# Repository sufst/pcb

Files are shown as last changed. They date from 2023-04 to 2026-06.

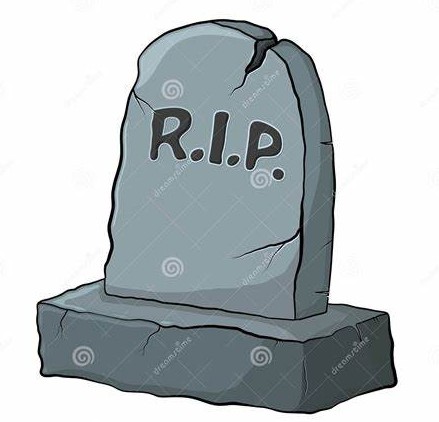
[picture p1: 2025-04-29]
common/images/RIP.jpg

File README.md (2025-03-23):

# PCBs

## About
Central repository of all schematics and PCB design files.

| Folder | Project | Project Code |
|---|---|---|
| ail | Accumulator Indicator Light Logic| `ail` |
| ail-led | Accumulator Indicator Light Led  | `ail-led` |
| batak | Batak Game (non-car) | `batak` |
| break-light| Rear Break Light | `break-light`|
| bspd | Brake System Plausibility Device | `bspd` |
| can-node | Voltage Reader and Broadcaster | `can-node` |
| curr-amp | Current Sensor Amplifier | `curr-amp` |
| dash | Dashboard | `dash` |
| discharge  | Discharge Relay Breakout | `discharge`  |
| hv-sense | High Voltage Sense | `hvs` |
| latching | Latch Circuit | `latching` |
| loom* | Loom Design | `loom` |
| lvbms | Low Voltage Battery Management System | `lvbms` |
| precharge  | Precharge Controller | `precharge`  |
| segment | Segment | `segment` |
| telemetry  | On-Car Telemetry | `telemetry`  |
| test-rig | PCB Test / Demo Rig | `test` |
| top-level* | Full Car Schematic | |
| trc | TSAC Relay Controller | `trc` |
| tsal | Tractive System Active Light | `tsal` |
| vcu | Vehicle Control Unit | `vcu` |

We design our PCBs in KiCad (version 8+).

>*Moved to https://github.com/sufst/loom

## Version Control for KiCad Projects

### Why?
- Revert individual changes.
- Document development history via commits and GitHub issues.
- Easily view previous versions of designs.
- Manage shared library of components.

### Files

Files that should be in this repo, under version control:
- Project files (`.kicad_pro`).
- Schematic files (`.kicad_sch`).
- PCB files (`.kicad_pcb`).
- Custom footprints (`.kicad_mod`).
- Custom symbols (`.kicad_sym`).
- Footprint library tables (`fp-lib-table`).
- Symbol library tables (`sym-lib-table`).
- 3D models of components (`.step` files).
- Simulation code (e.g. `.asc` files from LTSpice).

Files that should never be in here:
- Exports such as BOMs, gerbers, netlists, renders, etc.
- Local project settings (`.kicad_prl`).
- Project backups (.zip files generated in `<project name>-backups`, `.bak` `.bck` `-bak` files).
- Cache files (`fp-info-cache`).

The `.gitignore` should prevent the addition of files we don't want to keep in here, but before you commit make sure to do a quick check of what is actually being added.

### Shared Resources

The `common` folder is used for resources which can be shared across multiple projects. This includes:

- Images (`images` subdirectory).
- 3D models (`step` subdirectory).
- Custom symbols (`sufst-lib.kicad_sym`).
- Custom footprints (`sufst-lib.pretty`).
- SUFST standard sheet layout (`sheet-layout.kicad_wks`).

> Note: Since projects were previously in their own individual repos, many designs still have their own libraries, step files, etc. These will gradually be migrated to the SUFST library.

### Library Paths
When you configure the library paths for a project (`sym-lib-table` and `fp-lib-table` data), make sure to always use a path relative to the project with the `${KIPRJMOD}` substitution.

- Correct: `${KIPRJMOD}/../common/sufst-lib.kicad_sym`
- Incorrect: `/Users/<your name>/Documents/sufst/pcb/common/sufst-lib.kicad_sym`

If an absolute path is used, when someone else opens the project that path will not exist and the library paths will not be valid. `-lib-table` files should never contain an absolute path.

### Git Limitations
It is not possible to resolve merge conflicts within individual design files, which is an unfortunate limitation of using `git` with KiCad. While KiCad files are in a text format, they aren't really designed to be edited manually. It is therefore *essential* that only one person is editing a particular file in a project at a time (including the shared library). Once someone starts working on a file, until it is merged into the `main` branch nobody else can edit that file. A good way to get round this is to use the "hierarchical sheets" feature to divide schematics into multiple files (if it can be done in a logical way).

## Releases

### Release Files
When a PCB is fabricated, a new 'release' for the given project should be 
created and stored within this repo in the `releases/<PROJECT NAME>` folder. 
This folder should contain the latest version (and ONLY the latest version) of
the following files:

1. Exported gerbers and drill files in a ZIP archive called `fabrication.zip`.
2. Schematic sheets as a PDF (`Schematic.pdf`).
3. Layout as a PDF in colour, with border and title block (`Layout.pdf`).
4. HTML iBOM created using the ["Interactive HTML BOM Plugin"](https://github.com/openscopeproject/InteractiveHtmlBom) (`ibom.html`).

Additionally, a file called `info` (no extension) should be created (if it 
doesn't already exist) containing release information in the following format:

```txt
version: <VERSION NUMBER>
date: <RELEASE DATE>
fabrication: <COMPANY>
```

Version numbers should be in the format `v1.0.1` and dates should be in the
format `YYYY-MM-DD`. For example:

```txt
version: v1.0.1
date: 2023-01-23
fabrication: JLCPCB
```

The release folder for a project should then have the following structure and 
file names:

```txt
<PROJECT NAME>
├── Layout.pdf
├── Schematic.pdf
├── fabrication.zip
├── ibom.html
└── info
```

When creating a new release, make sure to overwrite/replace all the existing 
files.

### Release Tag

The release commit should then be tagged with the following command:

```sh
git tag <PROJECT CODE>-<VERSION_NUMBER>
```

Tagging should be done **after** merging to `main`! Example command:

```sh
git tag segment-v1.0.1
```

To push tags to GitHub:

```sh
git push --tags
```

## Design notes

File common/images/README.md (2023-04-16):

These images can be used to add SUFST graphics to PCB silkscreens using KiCad's bitmap2component app.

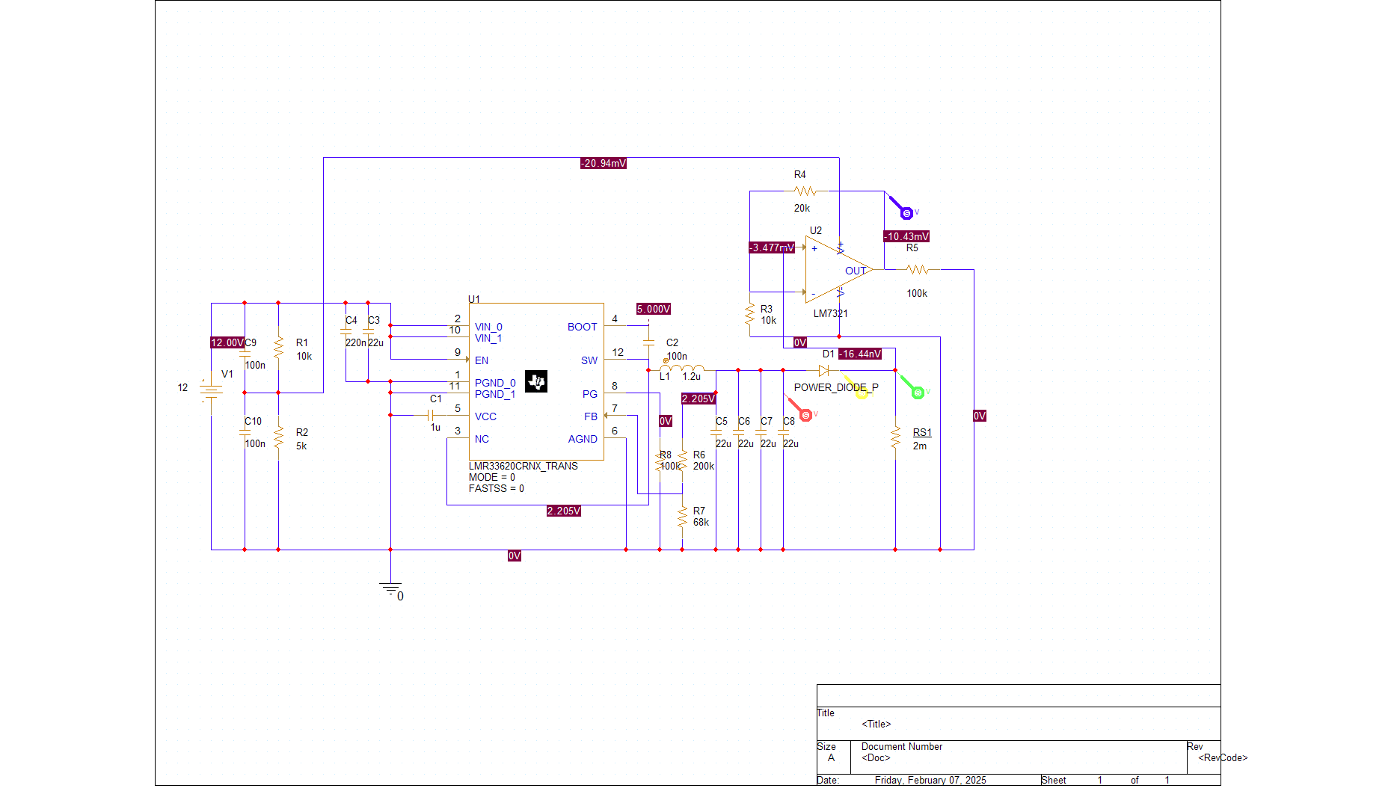
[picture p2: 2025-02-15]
tsal-led/sim/Pspice/tsal-led-driver/TSAL-LED-DRIVER.png

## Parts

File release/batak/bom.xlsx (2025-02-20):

Reference | Value | Datasheet | Footprint | Qty | Supplier | URL | Order Qty | Total Cost (£) | Notes
C1,C4 | 1uF | ~ | Capacitor_SMD:C_0603_1608Metric | 2 | Mouser |  |  |  | Already owned?
C2 | 10nF | ~ | Capacitor_SMD:C_0603_1608Metric | 1 | Mouser |  |  |  | Already owned?
C3,C8,C10 | 10uF | ~ | Capacitor_SMD:C_0603_1608Metric | 3 | Mouser |  |  |  | Already owned?
C5 | 470uF | ~ | Capacitor_THT:CP_Radial_D10.0mm_P5.00mm | 1 | Mouser | https://www.mouser.co.uk/ProductDetail/Vishay-BC-Components/MAL219056471E3 | 2 | 3.6 | Already owned?
C6,C9 | 100nF | ~ | Capacitor_SMD:C_0603_1608Metric | 2 | Mouser |  |  |  | Already owned?
C7 | 100uF | ~ | Capacitor_SMD:C_0603_1608Metric | 1 | Mouser |  |  |  | Already owned?
C11 | 180uF | ~ | Capacitor_THT:CP_Radial_D8.0mm_P3.50mm | 1 | Mouser | https://www.mouser.co.uk/ProductDetail/KEMET/A759KR187M1VAAE024 | 2 | 1.02 | Already owned?
D1 | YELLOW | ~ | LED_SMD:LED_0603_1608Metric | 1 | Mouser |  |  |  | Already owned?
D2 | GREEN | ~ | LED_SMD:LED_0603_1608Metric | 1 | Mouser |  |  |  | Already owned?
D3,D4,D6 | ESD9B3.3ST5G | https://www.onsemi.com/pub/Collateral/ESD9B-D.PDF | Diode_SMD:D_0603_1608Metric | 3 | Mouser | https://www.mouser.co.uk/ProductDetail/onsemi/ESD9B3.3ST5G?qs=yU2N9dt%252BrfmXrPf3vhgUEA%3D%3D | 10 | 0.76
D5 | BAT54W | https://assets.nexperia.com/documents/data-sheet/BAT54W_SER.pdf | Package_TO_SOT_SMD:SOT-323_SC-70 | 1 | Mouser | https://www.mouser.co.uk/ProductDetail/Taiwan-Semiconductor/BAT54W-RFG?qs=KwaGCOX4wIZBOfr1Otvg1A%3D%3D | 5 | 0.55 | Already owned?
IC1,IC2 | HT16K33 | https://www.holtek.com/webapi/116711/HT16K33Av101.pdf | sufst-lib:HT16K33 | 2 | AliExpress | https://www.aliexpress.com/item/1005007501060086.html | 5 | 3.79
J1 | USB_C_Receptacle_USB2.0_16P | https://www.usb.org/sites/default/files/documents/usb_type-c.zip | Connector_USB:USB_C_Receptacle_GCT_USB4105-xx-A_16P_TopMnt_Horizontal | 1 | Mouser | https://www.mouser.co.uk/ProductDetail/GCT/USB4105-GF-A-120?qs=QNEnbhJQKva%252Bjxw%2FpEjDhQ%3D%3D | 3 | 2.34
J2,J3,J4,J5,J6,J7,J8,J9,J10,J11,J12,J13 | Conn_01x04 | ~ | Connector_Molex:Molex_KK-254_AE-6410-04A_1x04_P2.54mm_Vertical | 13 |  |  |  |  | Already owned?
J14 | Conn_01x02 | https://docs.rs-online.com/accf/A700000008956731.pdf | Connector_AMASS:AMASS_XT60PW-F_1x02_P7.20mm_Horizontal | 1 |  |  |  |  | Already owned?
L1 | 68uH | ~ | Inductor_SMD:L_Coilcraft_MSS1210-XXX | 1 | Mouser | https://www.mouser.co.uk/ProductDetail/Coilcraft/MSS1210-683MED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 | 3 | 9.6
Q1,Q2 | NPN | https://ngspice.sourceforge.io/docs/ngspice-html-manual/manual.xhtml#cha_BJTs | Package_TO_SOT_SMD:SOT-23 | 2 | AliExpress | https://www.aliexpress.com/item/1005007360183764.html | 50 | 2.42 | 50PCS-SS8050-Y1
Q3,Q4,Q5,Q6,Q7,Q8,Q9,Q10,Q11,Q12,Q13,Q14,Q15,Q16,Q17 | NMOS | https://www.diodes.com/assets/Datasheets/ds11303.pdf | Package_TO_SOT_SMD:SOT-23 | 15 | AliExpress | https://www.aliexpress.com/item/1005006109969648.html | 100 | 2.44 | need to check voltage drop + current rating of specific model
R1,R2 | 1k | ~ | Resistor_SMD:R_0603_1608Metric | 14 | Mouser |  | 100 | 0.65 | Already owned?
R3,R4,R5,R8,R9,R22,R23,R24,R25,R26,R27,R28,R29,R30,R31,R32,R33,R34,R35,R36,R37 | 10k | ~ | Resistor_SMD:R_0603_1608Metric | 21 | Mouser |  | 100 | 0.65 | Already owned?
R6,R7 | 5.1k | ~ | Resistor_SMD:R_0603_1608Metric | 2 | Mouser |  | 100 | 0.65 | Already owned?
R10,R11,R12,R13,R14,R15,R16,R17,R18,R19,R20,R21,R38,R39 | 51k | ~ | Resistor_SMD:R_0603_1608Metric | 14 | Mouser |  | 100 | 0.65 | Already owned?
SW1,SW2 | BOOT, RESET | ~ | Button_Switch_SMD:SW_Push_1P1T_NO_CK_KMR2 | 2 |  |  |  |  | Already owned (for LVBMS)?
U1 | AP2112K-3.3 | https://www.diodes.com/assets/Datasheets/AP2112.pdf | Package_TO_SOT_SMD:SOT-23-5 | 1 | AliExpress | https://www.aliexpress.com/item/32998839398.html | 10 | 1.01
U2 | CH340C | https://datasheet.lcsc.com/szlcsc/Jiangsu-Qin-Heng-CH340C_C84681.pdf | Package_SO:SOIC-16_3.9x9.9mm_P1.27mm | 1 | AliExpress | https://www.aliexpress.com/item/1005006040438712.html | 5 | 1.87
U3 | XL1509-5.0 | https://datasheet.lcsc.com/lcsc/1809050422_XLSEMI-XL1509-5-0E1_C61063.pdf | Package_SO:SOIC-8_3.9x4.9mm_P1.27mm | 1 | AliExpress | https://www.aliexpress.com/item/1005003830233152.html | 10 | 1.2
U4 | ESP32-S3-WROOM-1 | https://www.espressif.com/sites/default/files/documentation/esp32-s3-wroom-1_wroom-1u_datasheet_en.pdf | RF_Module:ESP32-S3-WROOM-1 | 1 | Mouser | https://www.mouser.co.uk/ProductDetail/Espressif-Systems/ESP32-S3-WROOM-1-N16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 | 3 | 8.25 | Must be specifically the ESP32-S3-WROOM-1-N8 or ESP32-S3-WROOM-1-N16
U5,U6 | LTC-4627JR | http://optoelectronics.liteon.com/upload/download/DS30-2000-185/LTC-4627JR.pdf | Display_7Segment:LTC-4627Jx | 2 | Mouser | https://www.mouser.co.uk/ProductDetail/Lite-On/LTC-4627JR?qs=WxFF5lh7QM3%252BoGt5Rn2nWQ%3D%3D | 4 | 6.6
BZ1 | Buzzer | https://www.mouser.co.uk/datasheet/2/1628/cmi_1275_03th-3513223.pdf | sufst-lib:CUI_CMI-1275-85T | 1 | Mouser | https://www.mouser.co.uk/ProductDetail/Same-Sky/CMI-1275-03TH?qs=olJun0bQHM%252BIti8gD3qf0w%3D%3D | 3 | 2.34 | Already owned (Adam's kit)?
RV1 | 300k | https://www.mouser.co.uk/datasheet/2/54/3362-776956.pdf | sufst-lib:TRIM_3362P-1-304LF | 1 | Mouser | https://www.mouser.co.uk/ProductDetail/Bourns/3362P-1-304LF?qs=P4Be%2F1I712%2FfO%252BvhxotFeA%3D%3D | 3 | 2.58 | Already owned (for BPSD)?
SW3 | 0S102011MS2QN1 | https://www.ckswitches.com/media/1428/os.pdf | sufst-lib:0S102011MS2QN1 | 1 | Mouser | https://www.mouser.co.uk/ProductDetail/CK/0S102011MS2QN1?qs=xWNScUPc28o71osWFQSpZA%3D%3D | 3 | 1.08 | Already owned?
- | LED Buttons |  |  | 12 | AliExpress |  | 12 | 45 | 100mm or 60mm?
- | Start/Reset Buttons |  |  | 2 |  |  |  |  | Also needed for dash?

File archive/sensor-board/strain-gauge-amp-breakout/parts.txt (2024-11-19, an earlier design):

https://www.mouser.co.uk/ProductDetail/Texas-Instruments/REF2033AIDDCR?qs=7z%252BmIopC6%2FKHHOBVNaL7UQ%3D%3D
https://www.mouser.co.uk/ProductDetail/Analog-Devices/AD623ARMZ-REEL

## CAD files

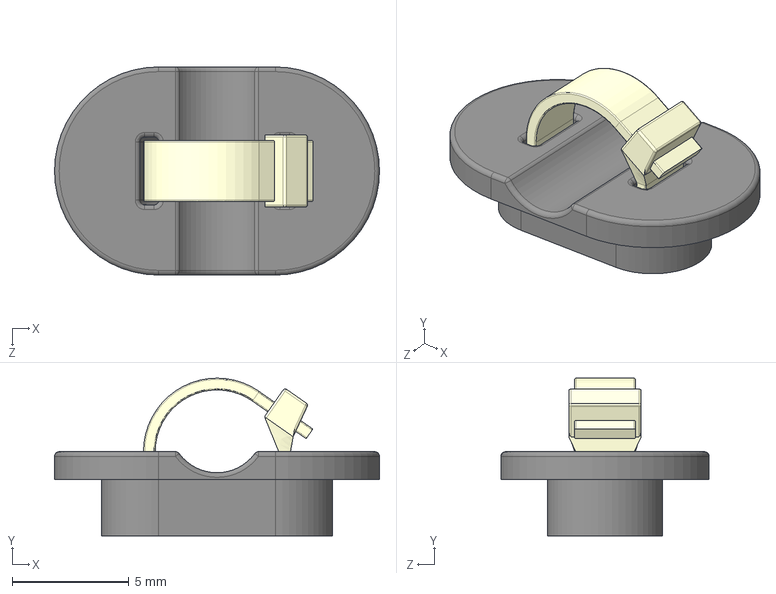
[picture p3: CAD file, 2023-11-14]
PCB - VOLTAGE TAPS/segment-pcb-ty-rap-assy.STEP
13.9 x 6.74 x 8.90 mm
segment-pcb-ty-rap-mount
segment-pcb-ty-rap

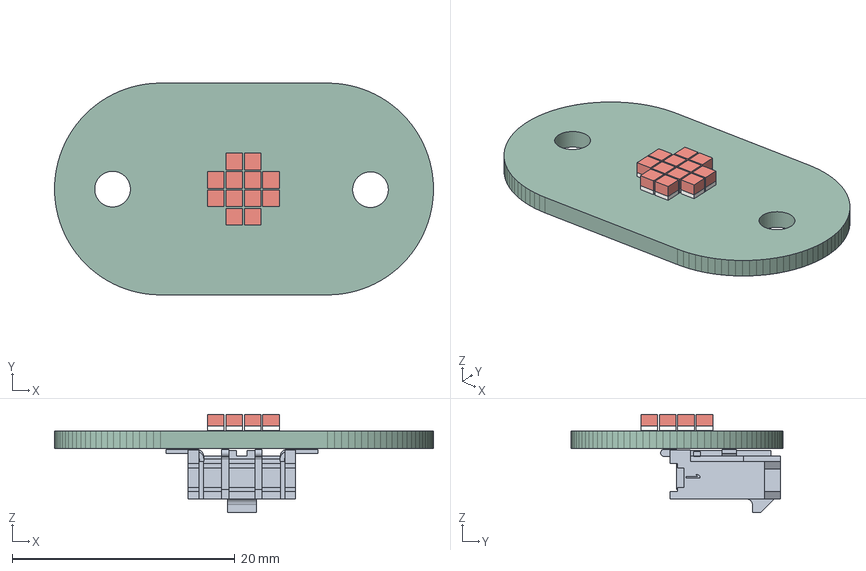
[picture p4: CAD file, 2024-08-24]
ail-LED/ail-LED.step
34.0 x 19.0 x 8.79 mm
(Unsaved) x 12
ail-LED PCB

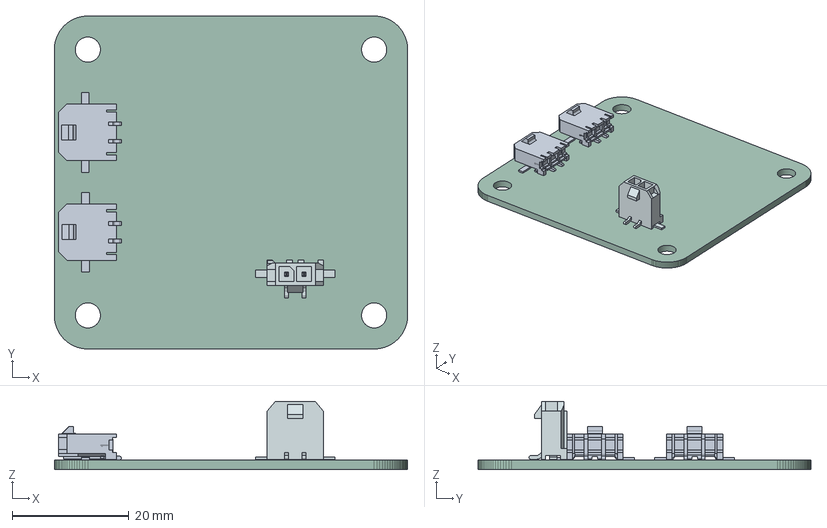
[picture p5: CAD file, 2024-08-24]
ail/ail.step
60.5 x 57.0 x 11.7 mm
436500224wbm000_01
ail PCB

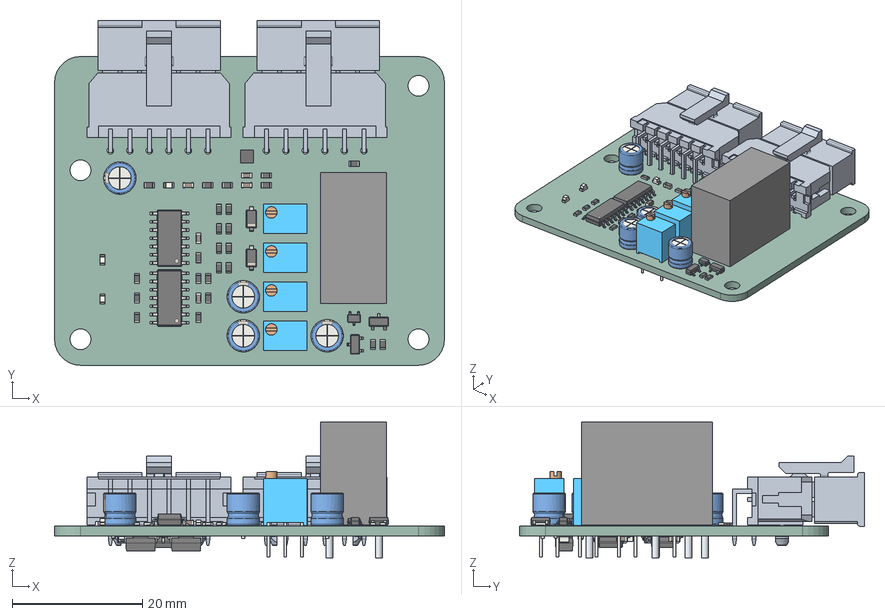
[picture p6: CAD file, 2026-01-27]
bspd/bspd v1.3.0.step
60.0 x 53.0 x 20.9 mm
R_0603_1608Metric x 32
D_SOD-123 x 2
CP_Radial_D5.0mm_P2.00mm x 4
SOT-323_SC-70 x 2
Potentiometer_Bourns_3266W_Vertical x 4
C_0603_1608Metric x 8
Leads
LED_0603_1608Metric x 3
SOIC-14_3.9x8.7mm_P1.27mm x 4
SOT-23 x 2
D_SMA x 2
BSPD_PCB

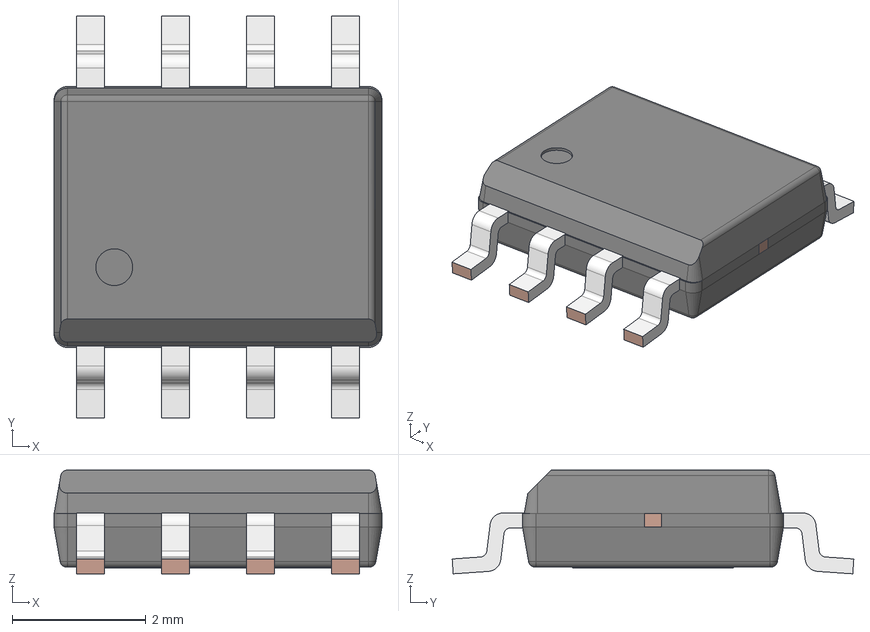
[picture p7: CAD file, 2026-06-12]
common/step/AP7375Q-33SP-13.stp
4.90 x 6.00 x 1.55 mm
CPD
LDF - outer lead
LDF - 8L-EP

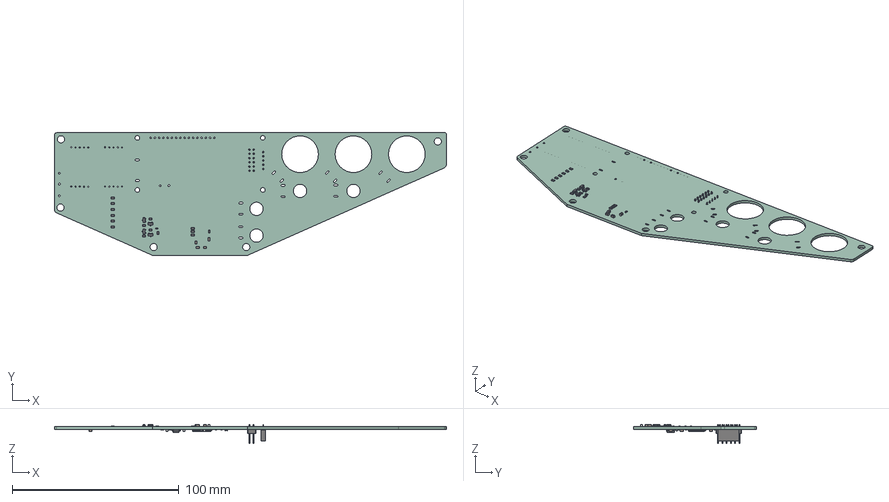
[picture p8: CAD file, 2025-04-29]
dash/Dash-PCB.step
235.0 x 73.6 x 11.6 mm
R_0805_2012Metric x 25
C_0805_2012Metric x 10
SOT_23 x 4
Fuse_0603_1608Metric x 2
PinHeader_2x06_P254mm_Vertical
C_0603_1608Metric x 3
SOIC_8_39x49mm_P127mm
TQFP_44_10x10mm_P08mm
PinSocket_1x05_P254mm_Vertical
Dash-PCB_PCB

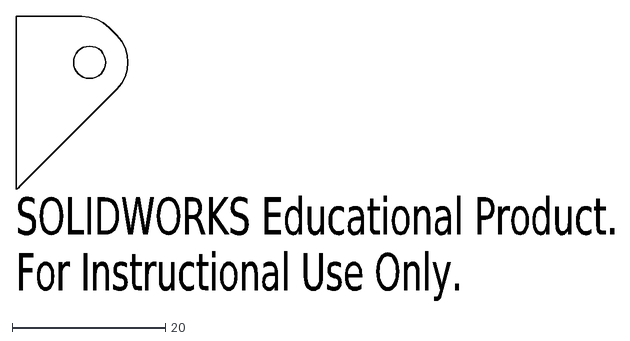
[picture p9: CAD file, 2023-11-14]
PCB - VOLTAGE TAPS/24-A02-212-0 - PART - THIN BUSBAR RH HOLE.DXF
SOLIDWORKS Educational Product.
For Instructional Use Only.

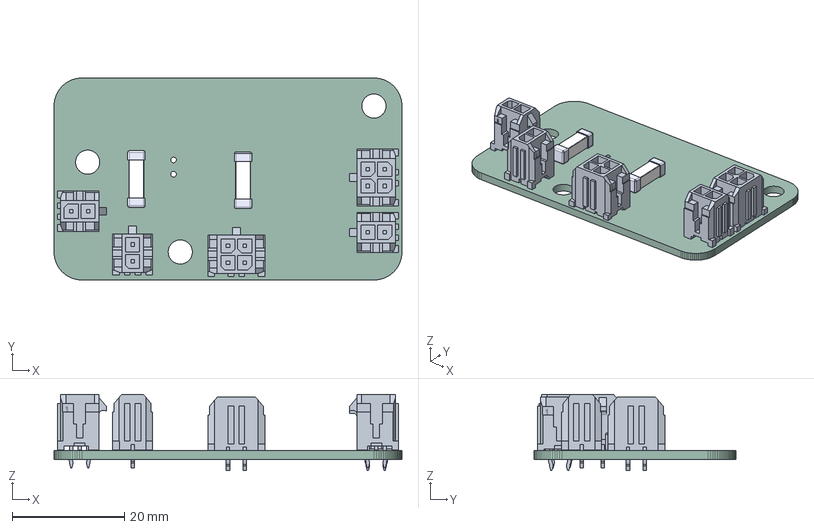
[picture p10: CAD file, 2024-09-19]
precharge/precharge.step
62.0 x 36.0 x 13.6 mm
0463020.ER x 2
precharge PCB

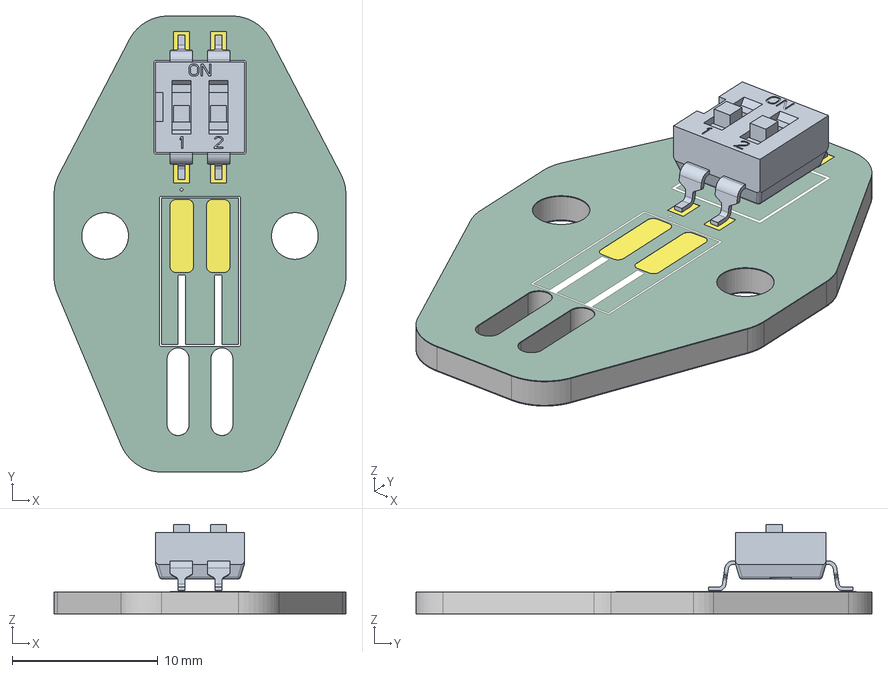
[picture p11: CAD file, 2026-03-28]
release/segment-scs/segment-scs-switch_v1.0.0.step
20.0 x 31.2 x 6.19 mm
segment-scs-switch_copper
segment-scs-switch_silkscreen
segment-scs-switch_soldermask
segment-scs-switch_PCB

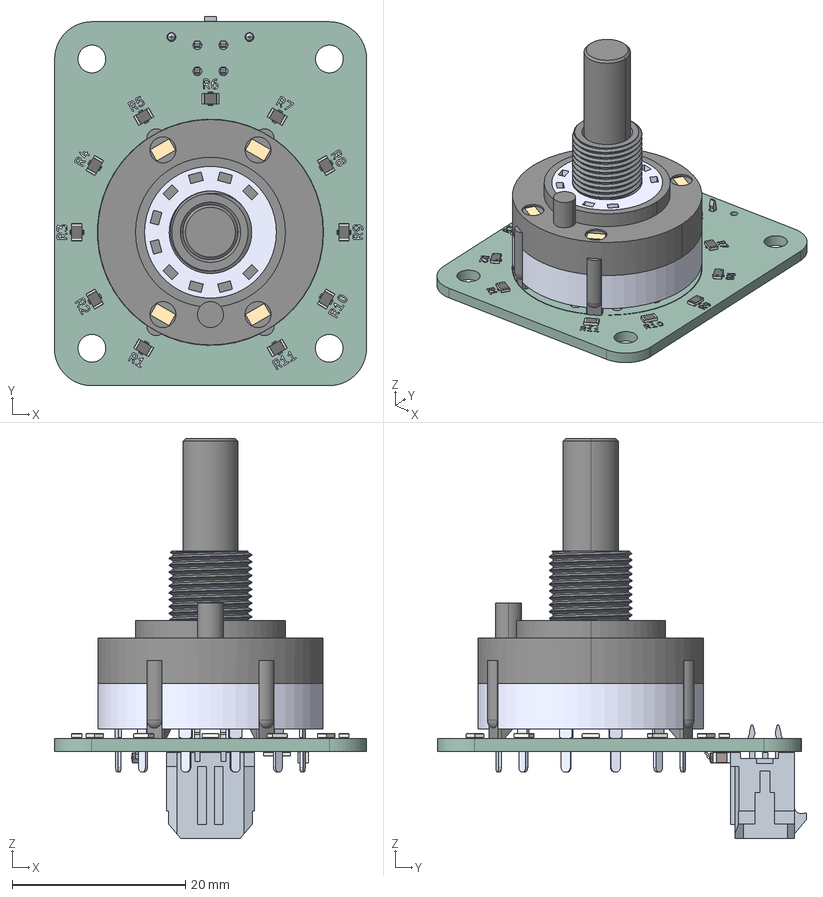
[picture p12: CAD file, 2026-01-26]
rotary-switch/rotary-switch_v1.0.0.step
36.0 x 42.6 x 46.1 mm
R_0805_2012Metric x 13
SR2612F-0112-21R0B-D8-N
D_SOD-123
C_0805_2012Metric
rotary-switch_silkscreen
rotary-switch_PCB

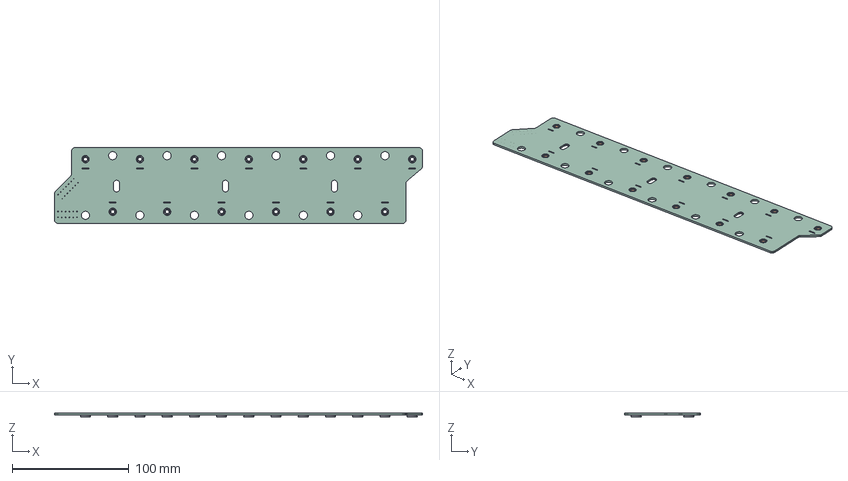
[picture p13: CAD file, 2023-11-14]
segment-stagx/PCB - VOLTAGE TAPS.step
314.9 x 65.0 x 3.58 mm
segment-stagx PCB

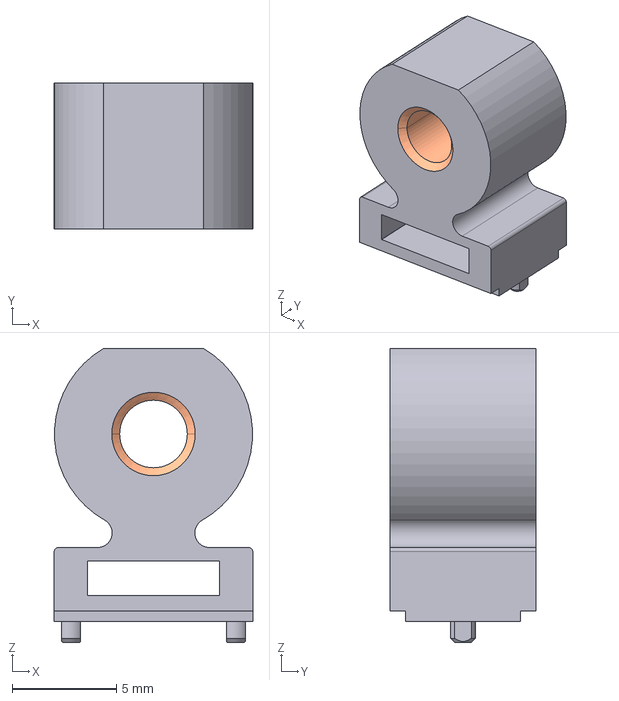
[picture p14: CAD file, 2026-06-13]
tem/SMTRAM4-9-7ET-PennEngineering-3D-11-02-2023.stp
9.53 x 7.00 x 14.1 mm

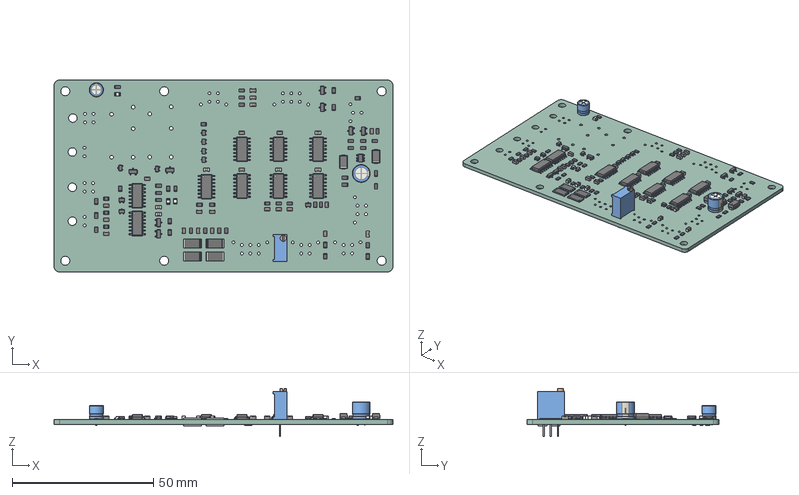
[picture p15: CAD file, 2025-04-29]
tsal-latching-integrated/tsal-latching-integrated.step
120.0 x 68.0 x 17.1 mm
R_0805_2012Metric x 50
SOT_323_SC_70 x 9
C_0805_2012Metric x 28
SOT_23 x 8
SOIC_14_39x87mm_P127mm x 9
D_SMA x 2
R_2512_6332Metric x 8
LED_0805_2012Metric x 3
SOT_23_6
CP_Radial_D50mm_P200mm
CP_Radial_D63mm_P250mm
Potentiometer_Bourns_3296W_Vertical
tsal-latching-integrated_PCB

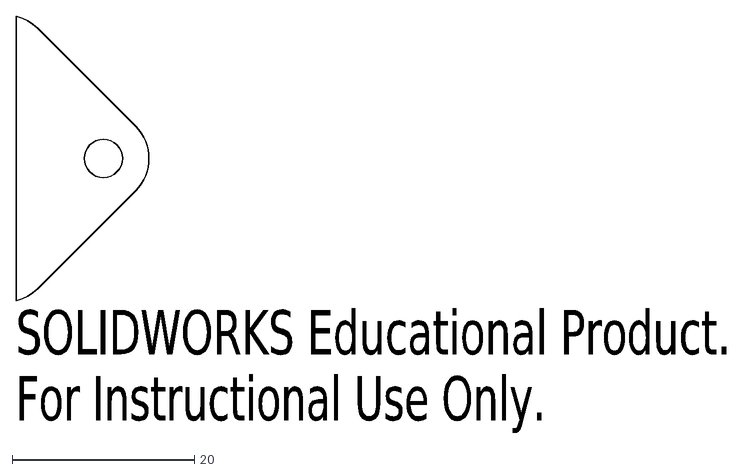
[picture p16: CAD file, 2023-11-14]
PCB - VOLTAGE TAPS/24-A02-211-0 - PART - STANDARD BUSBAR.DXF
SOLIDWORKS Educational Product.
For Instructional Use Only.

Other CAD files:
tem/DUMMY TEM PCB.DXF
PCB - VOLTAGE TAPS/24-A02-213-0 - PART - THIN BUSBAR LH HOLE.DXF
common/step/S1941-42R.stp
PCB - VOLTAGE TAPS/PCB - VOLTAGE TAPS.step
PCB - VOLTAGE TAPS/KFS2-M4-PennEngineering-3D-09-15-2023.stp
PCB - VOLTAGE TAPS/SMTSO-M4-2ET-PennEngineering-3D-09-16-2023.stp
PCB - VOLTAGE TAPS/segment-pcb-ty-rap-mount.STEP
common/step/01000066Z.stp
common/step/204-121.stp
common/step/2454985-2.stp
common/step/3214W-1-102G.stp
common/step/3362P-1-103LF.step
common/step/43020-1400.stp
common/step/43025-0400.stp
common/step/43025-1200.stp
common/step/43045-0412.stp
common/step/43045-1200.stp
common/step/43045-2400.stp
common/step/430451200.stp
common/step/43650-0410.stp
common/step/43650-0600.stp
common/step/732512200.stp
common/step/ABM8AIG-8.000MHZ-1Z-T.stp
common/step/ALPS-RK09K.step
common/step/AT06-12SA.stp
common/step/AntennaConnector.step
common/step/BM61276.STEP
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

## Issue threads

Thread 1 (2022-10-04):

feat(vcu): update to STM32-F746ZG board

t-bre, 2022-10-04:
### Description
Update schematic for STM32-F746ZG board.

### Requirements
<!-- to be ticked when met -->
- [x] New schematic for STM32-F746ZG connectors.
- [x] Remove third CAN transceiver.
- [x] Update connections from MCU to rest of board.

Closed 2022-11-18.

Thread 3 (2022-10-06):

bug(vcu): CAN transceiver not 3.3V compatible

t-bre, 2022-10-06:
### Description
Current CAN transceiver is not 3.3V compatible, and the MCU operates on 3.3V. Replace with a 3.3V transceiver.

t-bre, 2022-11-08:
Currently have MAX33040E, need to change to MAX33041EASA+.

Closed 2022-11-18.

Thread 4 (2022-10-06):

feat(vcu): replace DRS driver with timer pin output

t-bre, 2022-10-06:
### Description
DRS servo can be driven directly from a timer pin on the MCU, instead of with an extra driver chip.

### Requirements
<!-- to be ticked when met -->
- [x] Remove old driver chip.
- [x] Add DRS output pin to MCU.
- [x] Level shift DRS output.
- [x] Add DRS to connector.

## Additional Notes
The servo is 5V, so the 3.3V MCU output will need to be level shifted.

Closed 2022-11-26.

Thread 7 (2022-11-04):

bug(tsal): fp-lib-table contains user-specific paths

t-bre, 2022-11-04:
### Description
fp-lib-table for TSAL contains:

```text
(fp_lib_table
  (lib (name "footprints")(type "KiCad")(uri "/home/joe/pro/sufst/precharge/hardware/precharge/footprints.pretty")(options "")(descr ""))
)
```

This should be a path relative to the project, instead of an absolute path specific to one user.

Not sure if this breaks the PCB in some way?

### Steps To Reproduce
1. Look at contents of `tsal/fp-lib-table`.
2. Single entry in table with path specific to one user.

### Expected Behaviour
No absolute paths in table.

Mxrxk, 2022-12-09:
This doesn't break the PCB, I checked the issue and imported the footprints library correctly so the path should be relative for everyone now. That path should have been removed in the latest tsal feat.

Closed 2022-12-09.

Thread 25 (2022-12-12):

feat(segment): thicken traces between voltage taps inputs and fuses

t-bre, 2022-12-12:
### Description
Rough calculation assuming 5A fault current indicates traces need to be about twice as thick between the input voltage taps and the fuses.

### Requirements
<!-- to be ticked when met -->
- [ ] Thicken traces.

Closed 2023-01-28.

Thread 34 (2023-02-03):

bug(tsal): not enough connections for LED outputs

t-bre, 2023-02-03:
### Description
TSAL driver does not have enough output connections for LED strips. Need 2x for each colour.

### Expected Behaviour
LED connector changed from 4x1 to 4x2 connector.

Closed 2023-02-04.

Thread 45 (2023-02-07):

bug(vcu): Molex connectors should be reversed

t-bre, 2023-02-07:
### Description
Clips on Molex connectors are currently facing towards the inside of the board. This makes it harder to remove them.

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

### Expected Behaviour
Clips facing towards outside of board.

Closed 2023-03-05.

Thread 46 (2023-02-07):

bug(tsal): Molex connectors should be reversed

t-bre, 2023-02-07:
### Description
Clips on Molex connectors are currently facing towards the inside of the board. This makes it harder to remove them.

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

### Expected Behaviour
Clips facing towards outside of board.

Closed 2025-03-23.

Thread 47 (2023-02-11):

bug(latching): latching mechanic not working

Mxrxk, 2023-02-11:
### Description
The design using the D-type flip flops U1 seems to not be working. The potential culprits could be the power on state (POR) or the method in which U1 is wired.

A redesign is required.

### Steps To Reproduce
1. Connect power into the circuit using 12V supply
2. Connect the IMD_Ok signal into the board (J2 pin 2) and connect to 10V supply
3. Connect the IMD_OK_LATCHED signal to an oscilloscope (J3 pin 2)
4. Power on 12V and 10V simultaneously. You will notice that the latching will latch into the fault state (J3 pin 2 LOW). This issue persists even if the IMD_Ok signal is connected to the 12V supply to have a truly simultaneous connection in.
5. Power on 10V slightly earlier than 12V. You will notice that the latching will now latch in the no-fault state (J3 pin 2 HIGH). However when IMD_Ok signal is sent to the fault state, the circuit remains latched in the no-fault state.

### Environment
B16 tools and equipment

### Expected Behaviour
When turned on simultaneously, the circuit should boot up in a no-fault state given that no faults are detected. If a fault is detected, the circuit must latch in the fault state and remain latched even if the IMD_Ok state changes to the no fault state. Power cycling the circuit should remove the error given that the signal is in a no-fault state.

t-bre, 2023-03-01:
Maybe working, latch IC tested in isolation and behaves as expected. Requires further testing!

t-bre, 2023-03-28:
See #68 which was probably the cause of this.

Closed 2023-04-01.

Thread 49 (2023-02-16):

bug(vcu): 5V regulator tab is not ground

t-bre, 2023-02-16:
### Description
5V regulator tab is the regulator output and not ground. This causes a short to the large exposed copper pad. The net of the pad should be changed to 5V and a new (small) 5V plane created.

Closed 2023-03-02.

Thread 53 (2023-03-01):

feat(vcu): update DRS servo hardware to 12V

t-bre, 2023-03-01:
### Description
Change DRS servo control system to operate at 12V. Potentially add a current measurement mechanism for intelligent servo control. The 5V regulator can be removed, which will fix #49.

Closed 2023-03-02.

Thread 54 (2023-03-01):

bug(vcu): analogue inputs not buffered

t-bre, 2023-03-01:
### Description
Analogue inputs from the APPS need to be buffered as the current resistor divider design affects the transfer function of the sensor.

### Expected Behaviour
Unity gain op-amp buffers added to analogue input channels.

Closed 2023-03-02.

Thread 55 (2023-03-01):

bug(vcu): output optocoupler at 3.3V instead of 12V

t-bre, 2023-03-01:
### Description
Output shift optocouplers pull up to 3.3V instead of 12V.

### Expected Behaviour
Output shift optocouplers pull up to 12V.

Closed 2023-03-01.

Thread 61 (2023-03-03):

bug(?): `Molex-MicroFit-430450400.step` incorrectly named

t-bre, 2023-03-03:
### Description
`430450400` is a 2x2 dual row Molex connector ([product page](https://www.molex.com/molex/products/part-detail/pcb_headers/0430450400)), but the STEP file is the single row 4x1 connector.

### Expected Behaviour
Name is corrected and 3D model paths updated.

t-bre, 2023-03-03:
The 3D model with this name is actually the `436500400`.

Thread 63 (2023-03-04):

bug(bspd): brake plausibility comparator not powered

t-bre, 2023-03-04:
### Description
Brake plausibility sheet comparator IC is not powered.

### Expected Behaviour
Power supply connection and decoupling capacitor added.

Closed 2023-04-03.

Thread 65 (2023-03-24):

bug(bspd): bad footprint for transistor

t-bre, 2023-03-24:
### Description
The footprint for the transistor which is used in the following circuit is wrong:

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

The footprint is BCE, but most transistors we have (BC557, 2N3906) are CBE.

### Expected Behaviour
Footprint changed to CBE.

Closed 2023-04-03.

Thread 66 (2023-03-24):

feat(bspd): add indicator LEDs

t-bre, 2023-03-24:
### Description
Add LEDs to indicate key states in the BSPD:
- SCS implausible (red, on during fault).
- Brake and throttle pressed (red, on during fault).
- Shutdown output state (green, on if shutdown circuit closed).

### Additional Notes
SMD LEDs on the PCB and one external LED on the BSPD box (via connector).

Closed 2023-04-03.

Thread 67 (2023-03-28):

feat(latching): add labels

t-bre, 2023-03-28:
### Description
PCB is currently un-labelled, would be nice to add:
- Connector names on the top of the board.
- Pin names on the bottom of the board.
- The project name and version number.
- SUFST stag logo (if space).

Closed 2023-04-02.

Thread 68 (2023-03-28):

bug(latching): signals latch to wrong state

t-bre, 2023-03-28:
### Description
Latching behaviour is the opposite of what we want, currently the output latches high when leaving the fault state and entering the "ok" state.

### Expected Behaviour
Output latches low when leaving "ok" state and entering fault state.

### Additional Notes
The inputs from the BMS and IMD need to be inverted and `Q'` of the latches used as the output. `Q = 1` should represent a fault state and `Q = 0` should represent an "ok" state.

Closed 2023-04-01.

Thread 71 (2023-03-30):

feat(latching): change connector orientation to horizontal

t-bre, 2023-03-30:
### Description
Connectors are currently vertical, it is better for them to be horizontal to reduce height / simplify routing in the junction box.

t-bre, 2023-04-01:
Connectors are already horizontal!

Closed 2023-04-01.

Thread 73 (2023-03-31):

feat(vcu): add connections for shield grounds

t-bre, 2023-03-31:
### Description
Shielded cables coming into the VCU need a connection to LVS ground. This can be provided through an extra/unused pin on the connectors.

Closed 2023-04-04.

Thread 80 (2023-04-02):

bug(hvs): missing symbols

t-bre, 2023-04-02:
### Description
Some symbols were missing after migration from the old separate PCB repos to this new monorepo. The schematic / PCB are fine, but these should be sorted eventually.

### Additional Notes
Causes ERC errors below:

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

t-bre, 2023-04-02:
Pretty sure the isolator can just be fixed by the "update symbol from library" button if you double click on the symbol in the schematic.

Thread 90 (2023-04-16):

feat(vcu): label power input polarity on front silkscreen

t-bre, 2023-04-16:
### Description
It would be useful to show the polarity of the power input connection on the front silkscreen. Currently it is only labelled on the back.

### Additional Notes
This definitely used to be on older designs, but must have accidentally been removed at some point.

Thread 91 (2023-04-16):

bug(vcu): button connections not identified on silkscreen

t-bre, 2023-04-16:
### Description
Button connections are not labelled on the back silkscreen as shown in screenshot below. Would be good to do it the same way as the LEDs.

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

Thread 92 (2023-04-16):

bug(vcu): EEPROM IC orientation not clear on silkscreen

t-bre, 2023-04-16:
### Description
When soldering the board, it is hard to tell what the correct orientation of the EEPROM IC is. There is a small dot, but it's not immediately obvious because it really is tiny. Might be good to add a larger dot/circle below pin 1. The reference designator for the IC is also on the opposite side to the dot, which could be incorrectly interpreted as the side of pin 1 if the dot isn't seen.

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

Closed 2025-02-20.

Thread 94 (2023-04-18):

chore: update to KiCad 7

t-bre, 2023-04-18:
### Description

Opening projects created in KiCad 6 with KiCad 7 causes a change to the project file which may be accidentally committed if the project is opened for reference when working on something else. To avoid merge conflicts caused by this, we should probably just open everything in KiCad 7 once and commit the changes.

Closed 2023-04-27.

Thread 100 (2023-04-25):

bug(hvs): incorrect silkscreen for PS1

Scaniox, 2023-04-25:
### Description
ps1 part has incorrect orientation of silk screen, but polarity is correct

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

Closed 2023-04-29.

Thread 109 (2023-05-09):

bug(bspd): shutdown connector silkscreen swapped

saltyboi2995, 2023-05-09:
### Description
Shutdown_in and shutdown_out connectors have silkscreens swapped

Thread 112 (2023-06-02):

bug(vcu): R2D and VC LED outputs swapped

t-bre, 2023-06-02:
### Description
The VCU has the R2D and VC LED outputs swapped.

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

### Additional Notes

Small schematic error, easily fixed in a future revision. This has been patched in software for now, remember that it will need to be changed if this is fixed on the PCB.

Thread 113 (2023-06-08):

bug(hvs): non-standard resistor values

t-bre, 2023-06-08:
### Description
The resistor values used to divide down the HV are very non-standard and not generally stocked at the university. They should ideally be replaced with values which are more common.

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

t-bre, 2023-06-08:
453k (x5) + 348k can be substituted quite closely with 470k (x5) + 270k

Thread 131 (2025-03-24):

bug(actions): ERC and DRC missing symbols

maartin0, 2025-03-24:
See the warnings in <https://github.com/sufst/pcb/actions/runs/14020534515/job/39251883864> for an example

Closed 2025-03-26.

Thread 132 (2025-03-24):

bug(actions): auto generate release files action incorrectly fails permission check

maartin0, 2025-03-24:
See the message [here](https://github.com/sufst/pcb/pull/130#issuecomment-2746280261) and the corresponding skipped action [here](https://github.com/sufst/pcb/actions/runs/14020536377).

Problematic line: <https://github.com/sufst/pcb/actions/runs/14020536377/workflow#L15>

It might be worth sending a message on success/failure rather than failing silently

Closed 2025-04-05.

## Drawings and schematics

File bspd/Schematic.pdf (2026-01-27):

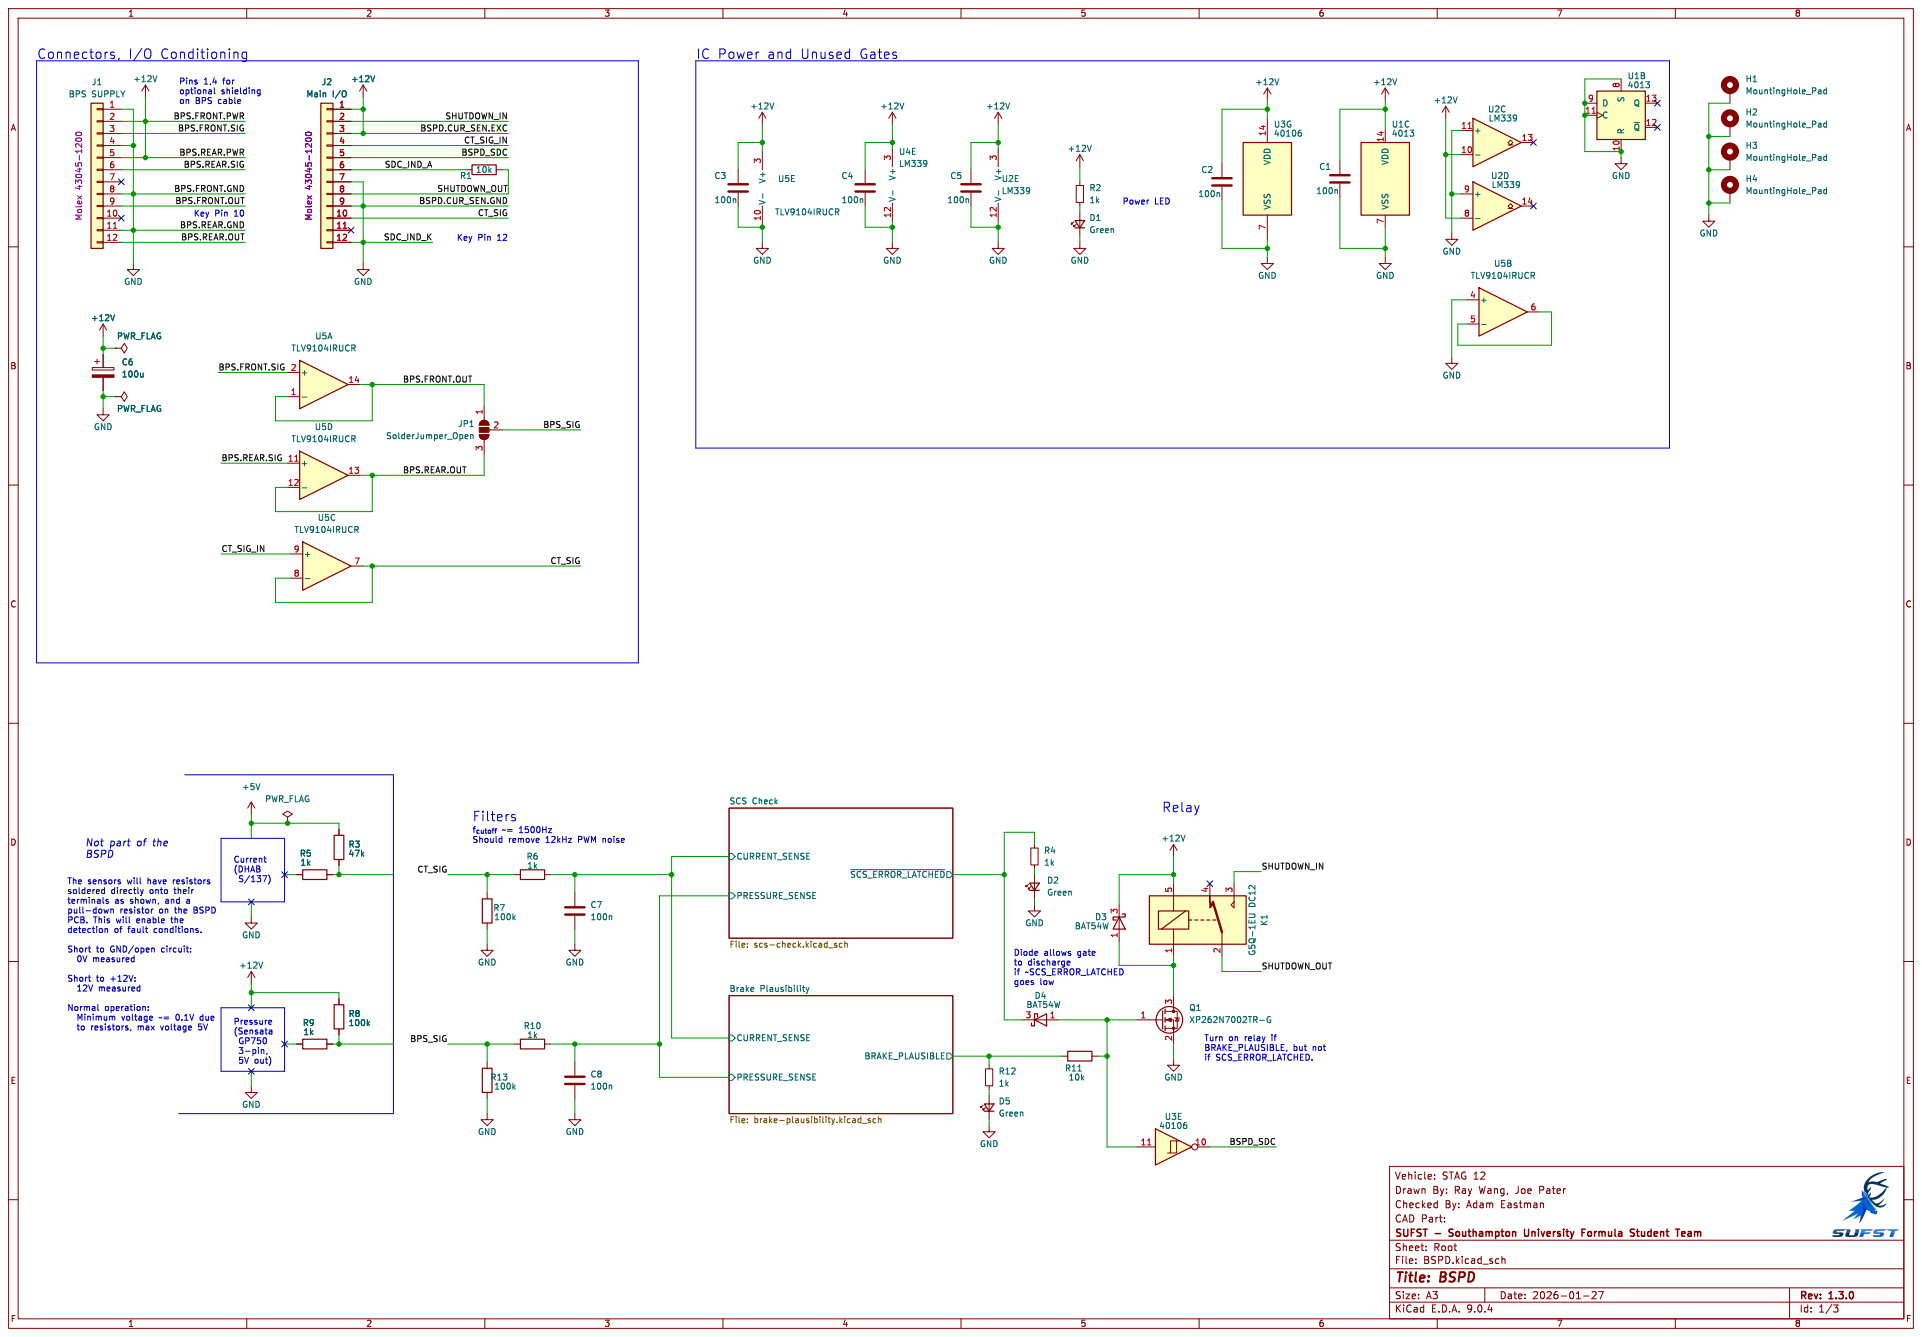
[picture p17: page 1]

IC Power and Unused Gates

BPS.FRONT.OUT BPS.FRONT.PWR
BPS.FRONT.SIG

SHUTDOWN_OUT BPS.FRONT.OUT BPS.REAR.GND

~{SCS_ERROR_LATCHED} SCS Check File: scs-check.kicad_sch CURRENT_SENSE

f_{cutoff}~= 1500Hz Should remove 12kHz PWM noise

The sensors will have resistors
PCB. This will enable the

Brake Plausibility File: brake-plausibility.kicad_sch

Turn on relay if BRAKE_PLAUSIBLE, but not
40106 GND

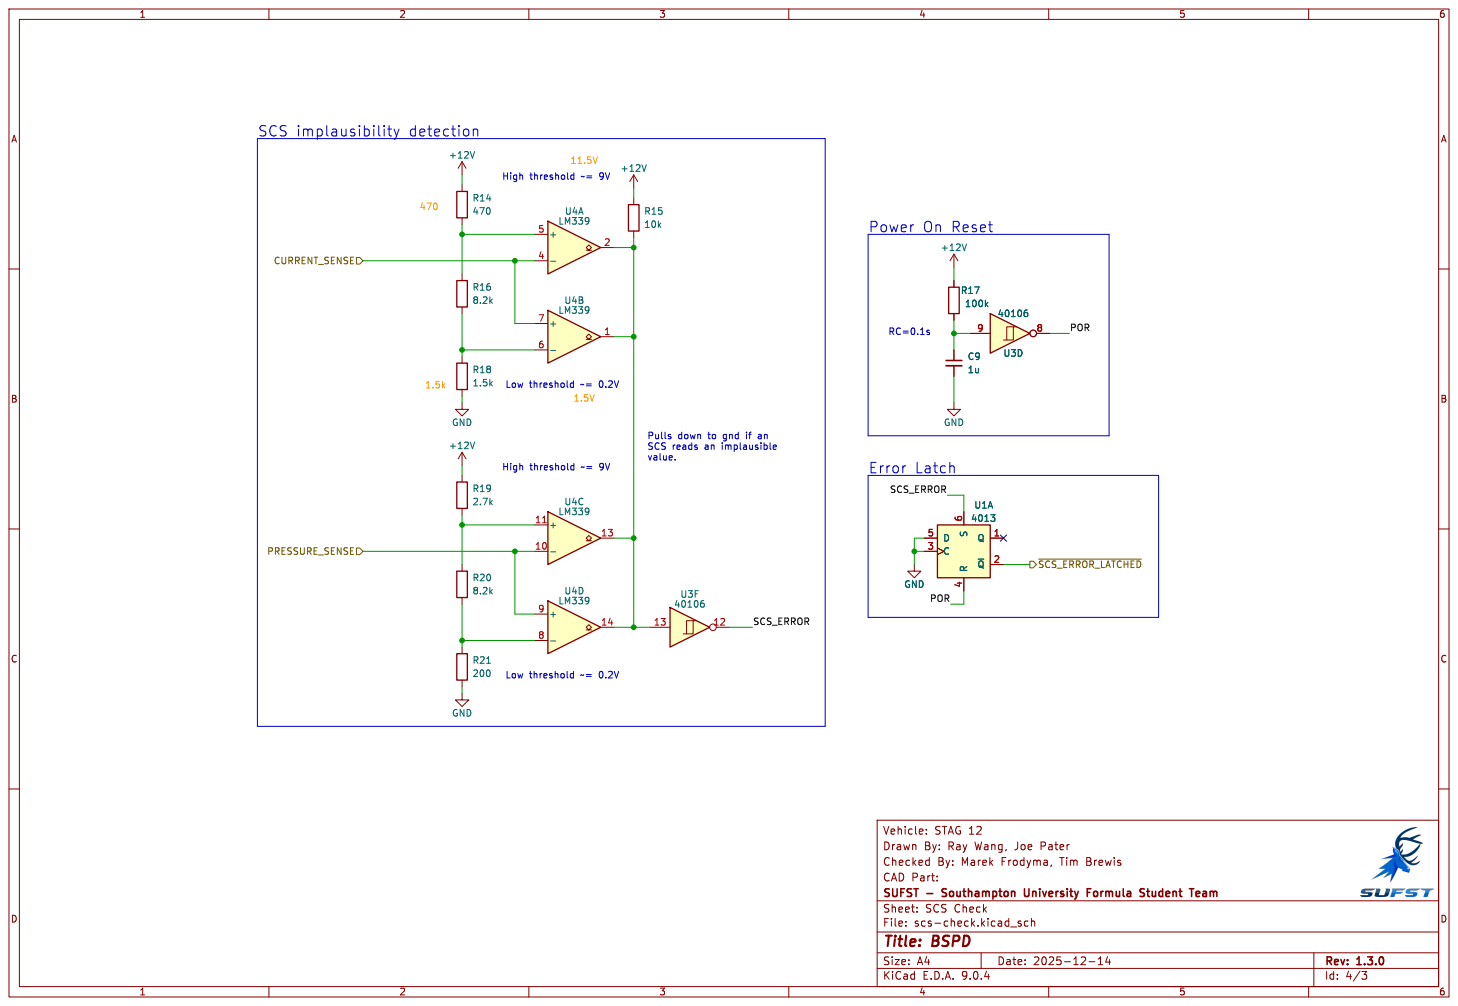
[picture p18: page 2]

Pulls down to gnd if an SCS reads an implausible

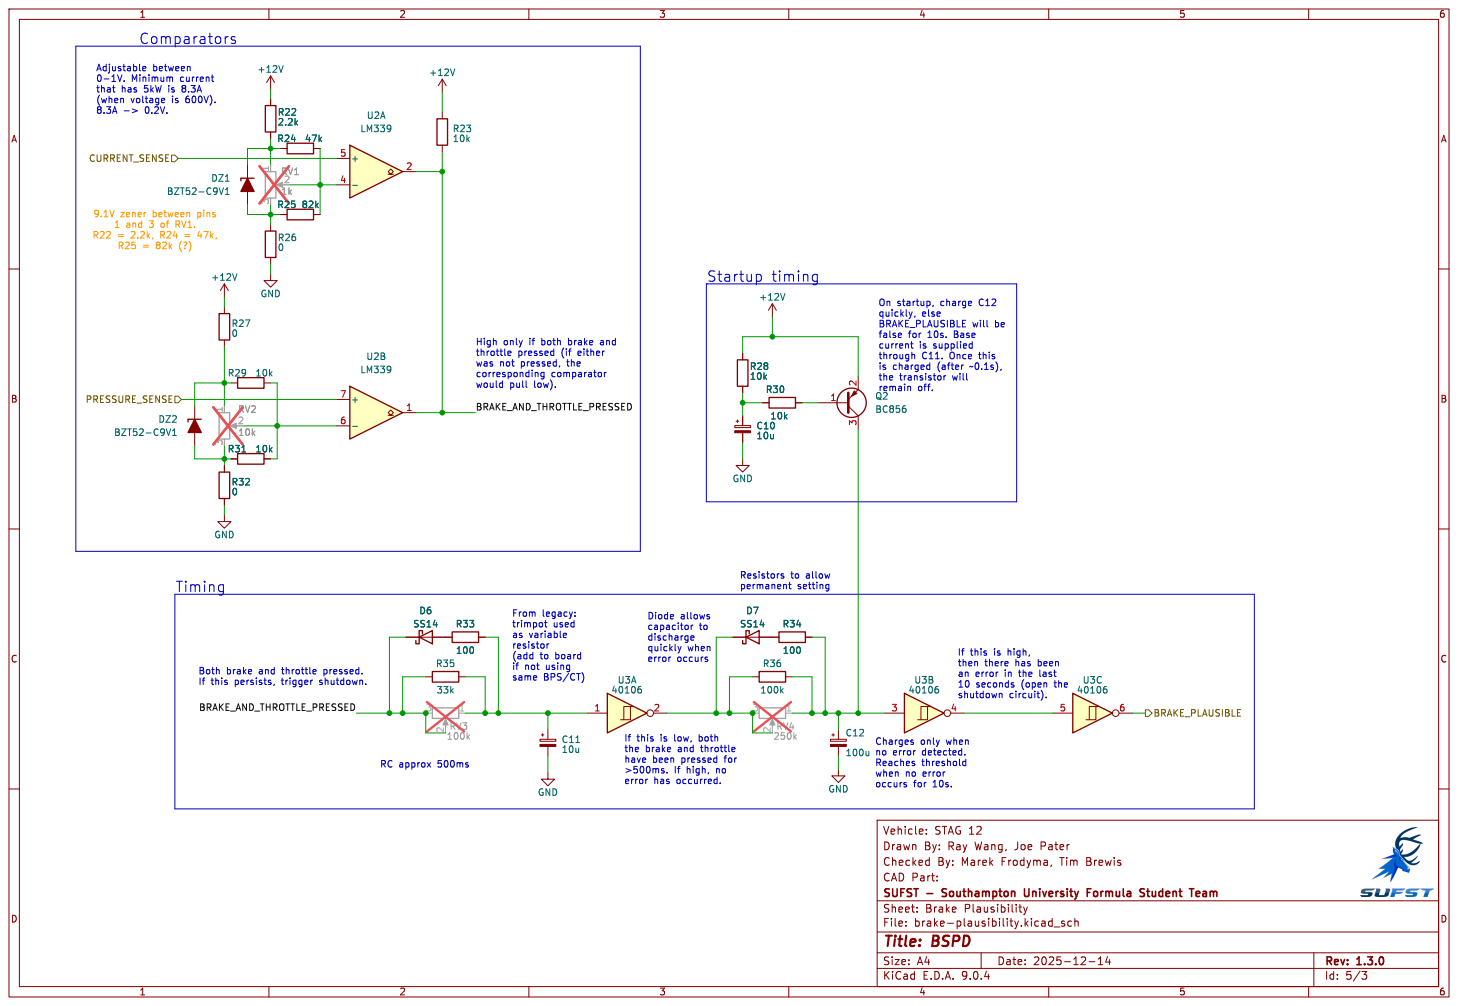
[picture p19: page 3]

error has occurred. Timing

If this is high,
then there has been
an error in the last 10 seconds (open the

If this is low, both
the brake and throttle

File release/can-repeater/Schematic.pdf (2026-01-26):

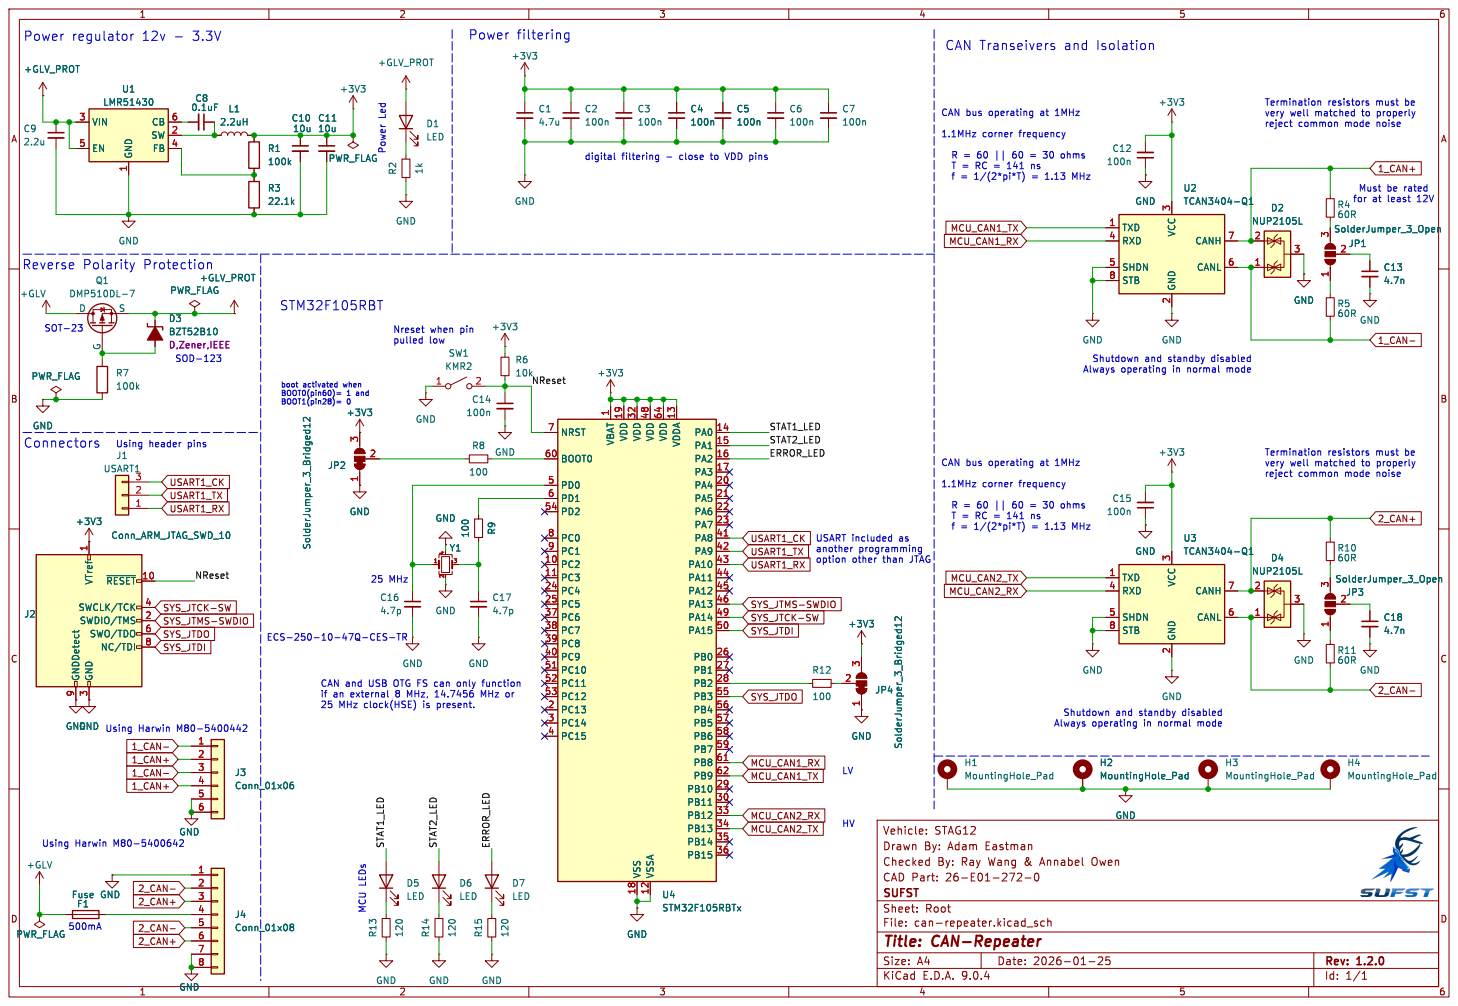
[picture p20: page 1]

reject common mode noise CAN and USB OTG FS can only function
10uPWR_FLAG

very well matched to properly

2 CANH 7 CANL 6 U3 TCAN3404-Q1 H3 MountingHole_Pad GND GND R21k D1

1 VDD 19 VDD 32 VSS 18 VDD 48 VSSA 12 VDD 64 VDDA 13 PA0 14 PA1 15 PA2 16 PA3 17 PA4 20 PA5 21 PA6 22 PA7 23 PA8 41 PA9 42 PA10 43 PA11 44 PA12 45 PA13 46 PA14 49 PA15 50 PB0 26 PB1 27 PB2 28 PB3 55 PB4 56 PB5 57 PB6 58 PB7 59 PB8 61 PB9 62 PB10 29 PB11 30 PB12 33 PB13 34 PB14 35 PB15 36 GND GND

1 VDD 19 VDD 32 VSS 18 VDD 48 VSSA 12 VDD 64 VDDA 13 PA0 14 PA1 15 PA2 16 PA3 17 PA4 20 PA5 21 PA6 22 PA7 23 PA8 41 PA9 42 PA10 43 PA11 44 PA12 45 PA13 46 PA14 49 PA15 50 PB0 26 PB1 27 PB2 28 PB3 55 PB4 56 PB5 57 PB6 58 PB7 59 PB8 61 PB9 62 PB10 29 PB11 30 PB12 33 PB13 34 PB14 35 PB15 36 U4STM32F105RBTx R10

3 ~{RESET}10 SWCLK/TCK 4 SWDIO/TMS 2 SWO/TDO 6 NC/TDI 8 GND GND

reject common mode noise

option other than JTAG
JP4 SolderJumper_3_Bridged12 1

3 ~{RESET}10 SWCLK/TCK 4 SWDIO/TMS 2 SWO/TDO 6 NC/TDI 8

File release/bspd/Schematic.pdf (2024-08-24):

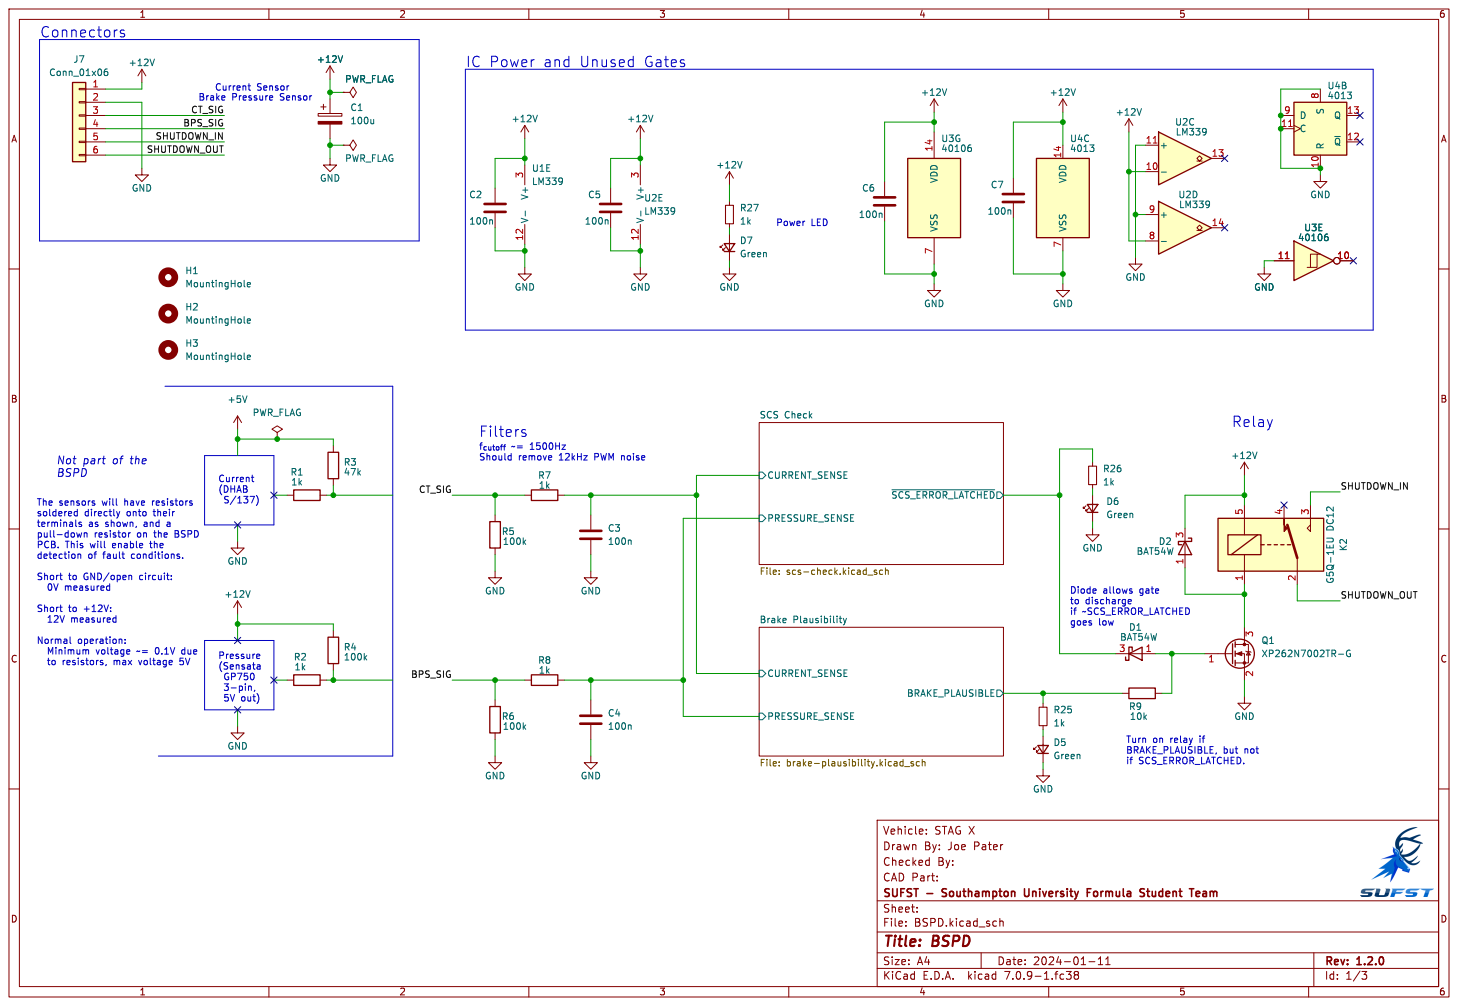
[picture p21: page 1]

Brake Pressure Sensor Current Sensor Current (DHAB

IC Power and Unused Gates

~{SCS_ERROR_LATCHED} SCS Check File: scs-check.kicad_sch CURRENT_SENSE

S/137) Not part of the BSPD

The sensors will have resistors
PCB. This will enable the

Brake Plausibility File: brake-plausibility.kicad_sch

Turn on relay if BRAKE_PLAUSIBLE, but not

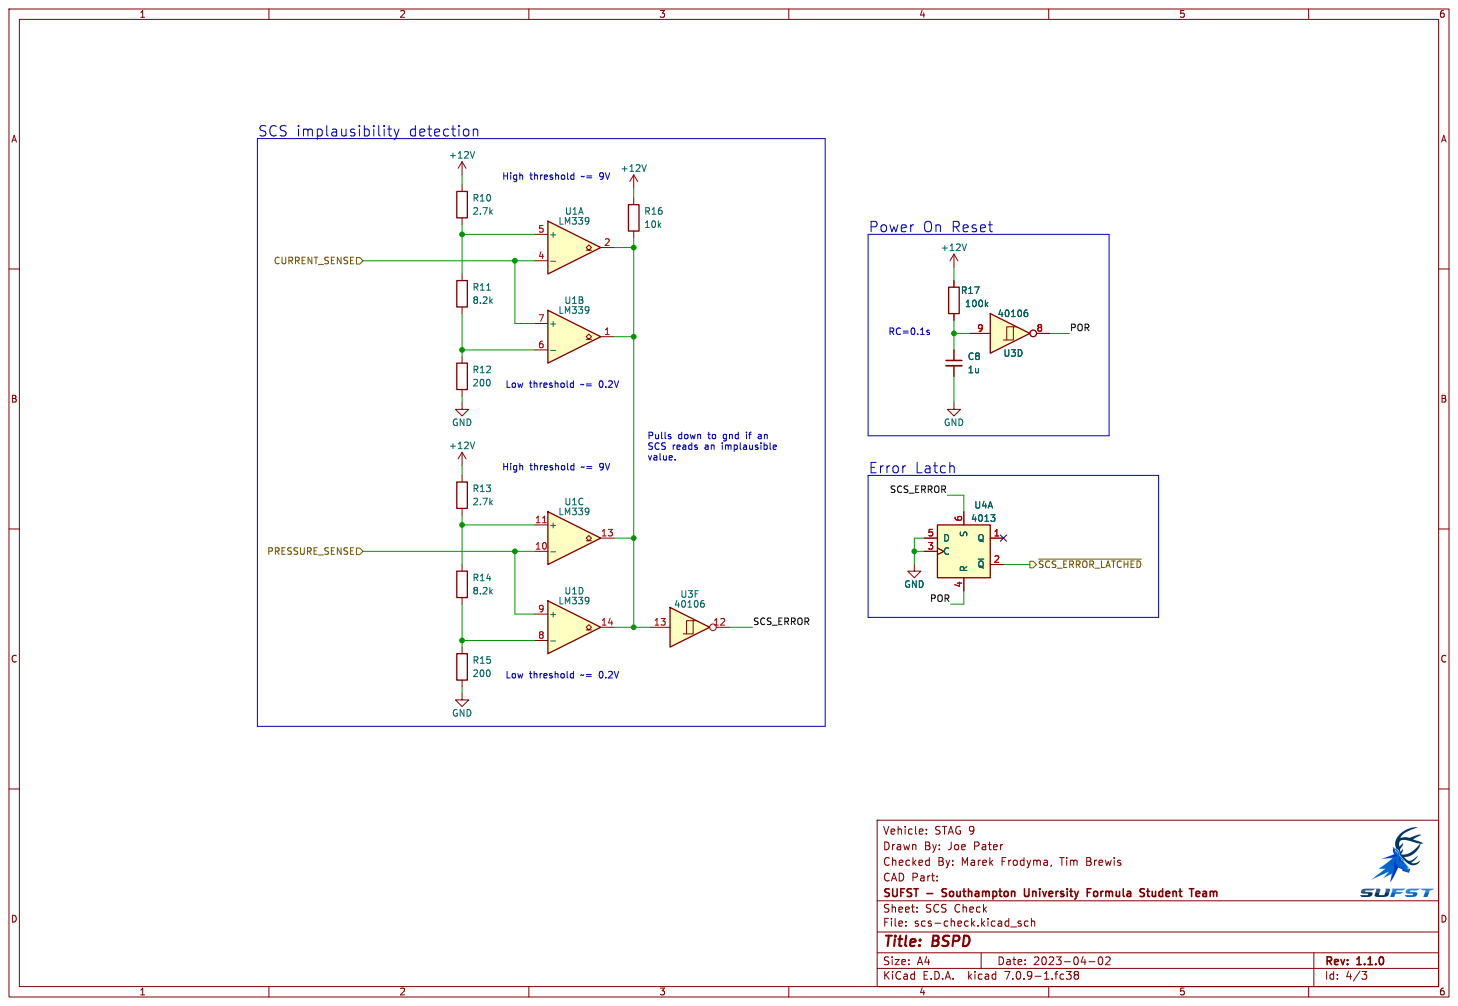
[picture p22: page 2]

Pulls down to gnd if an SCS reads an implausible

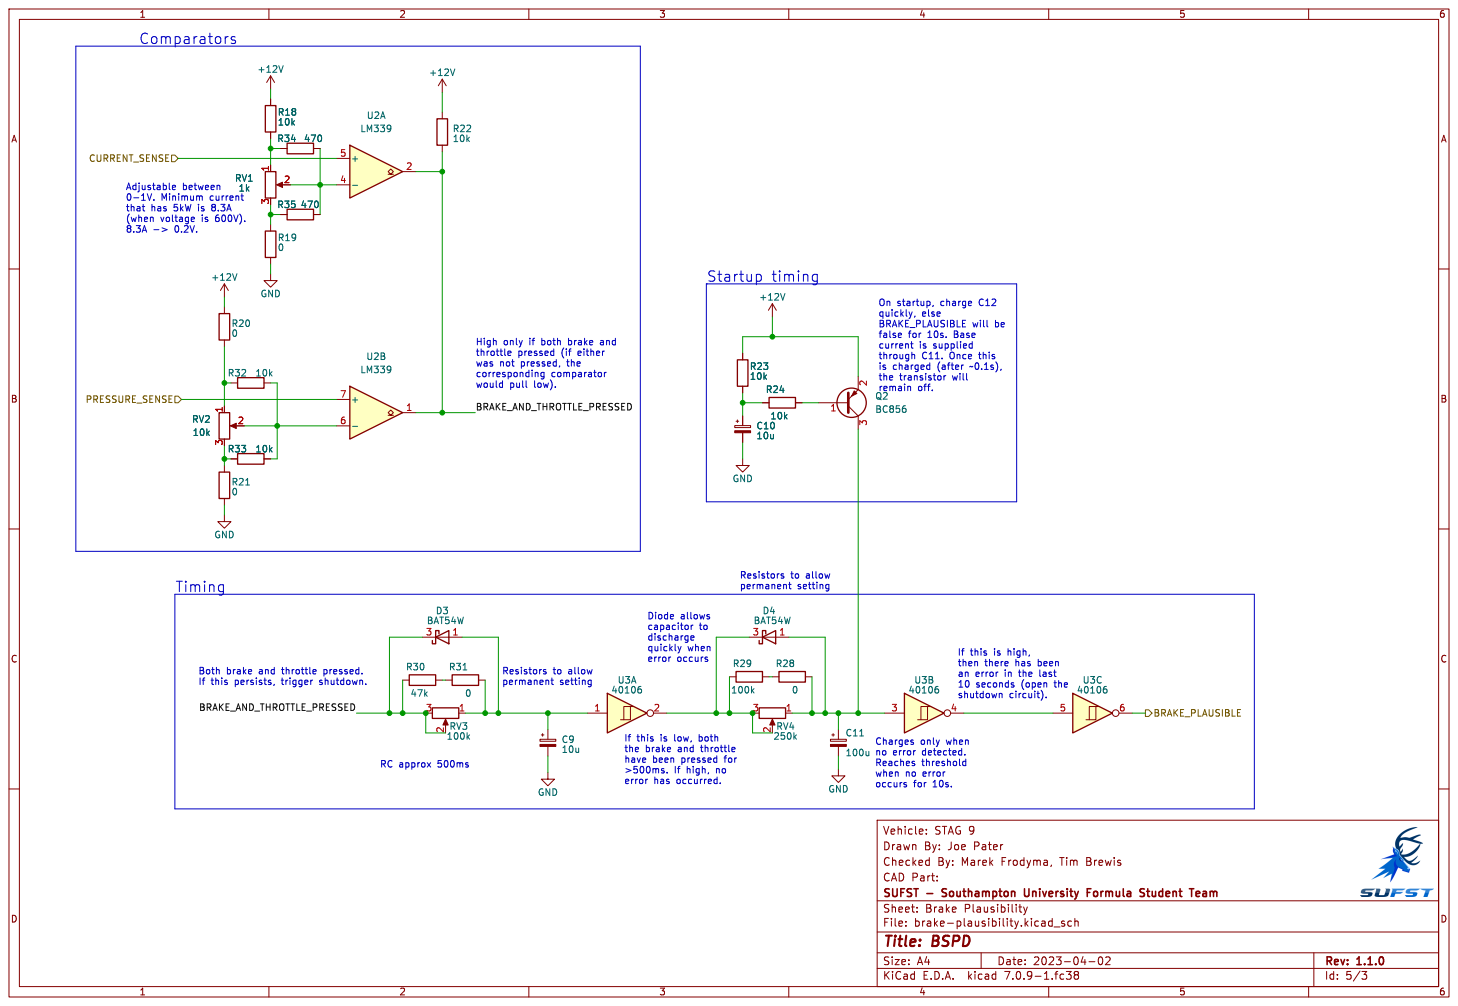
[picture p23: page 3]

High only if both brake and

shutdown circuit). Diode allows
discharge
quickly when

If this is high,
then there has been
an error in the last 10 seconds (open the

If this is low, both
the brake and throttle

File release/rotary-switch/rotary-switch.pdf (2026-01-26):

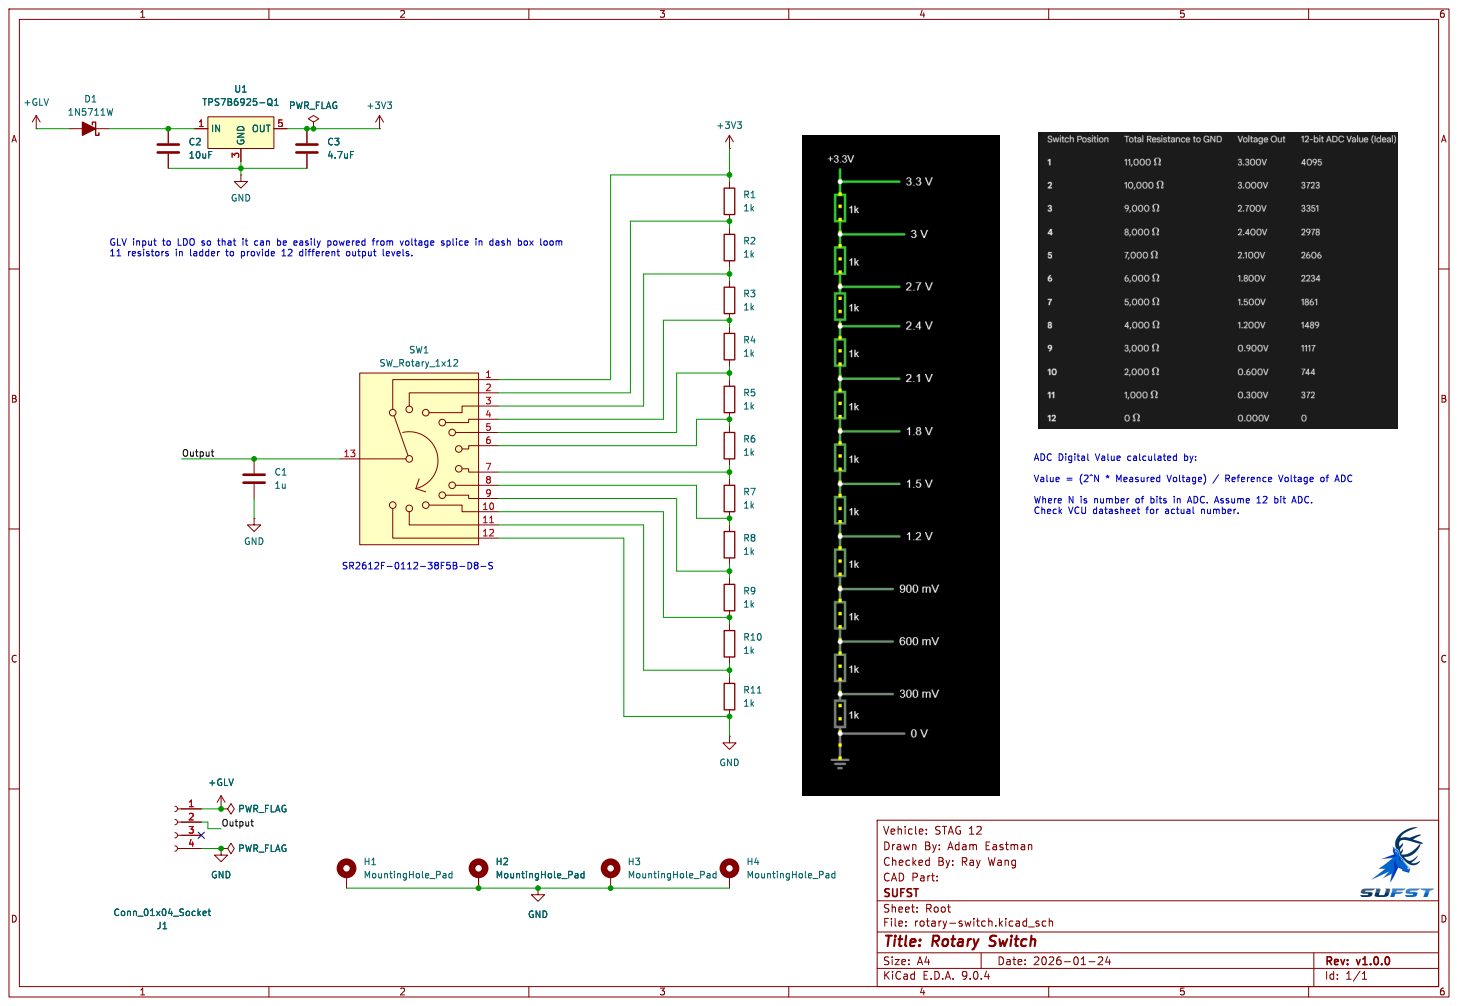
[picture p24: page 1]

Output GLV input to LDO so that it can be easily powered from voltage splice in dash box loom

Id: 1/1 Title: Rotary Switch

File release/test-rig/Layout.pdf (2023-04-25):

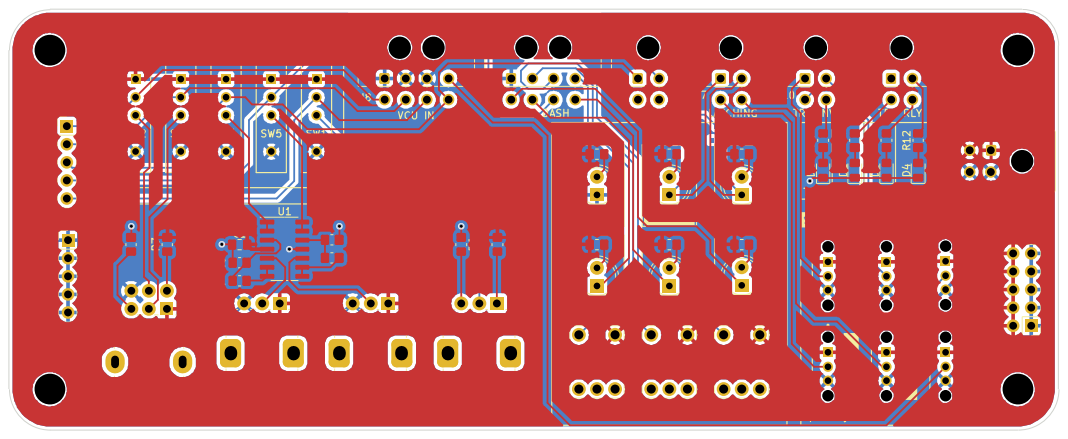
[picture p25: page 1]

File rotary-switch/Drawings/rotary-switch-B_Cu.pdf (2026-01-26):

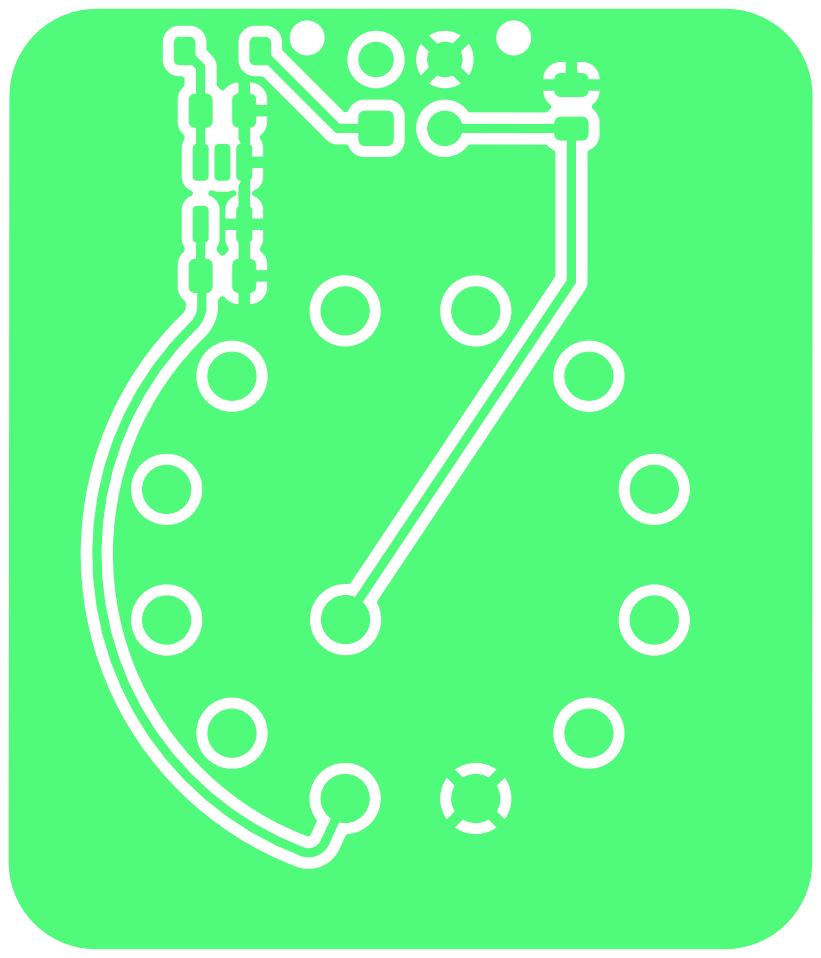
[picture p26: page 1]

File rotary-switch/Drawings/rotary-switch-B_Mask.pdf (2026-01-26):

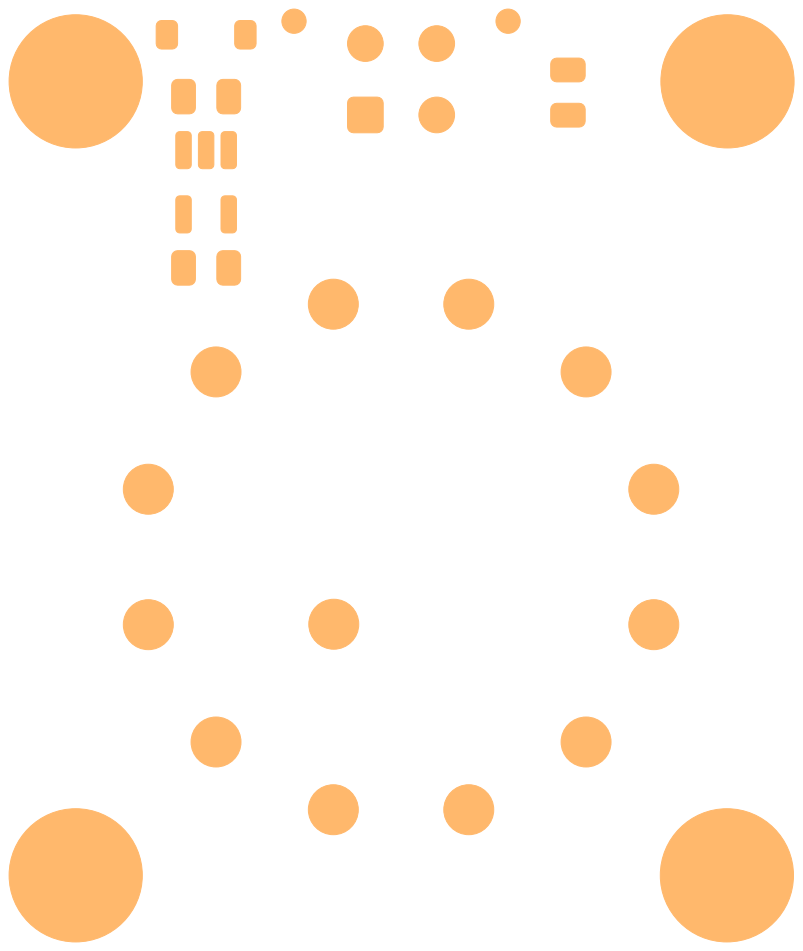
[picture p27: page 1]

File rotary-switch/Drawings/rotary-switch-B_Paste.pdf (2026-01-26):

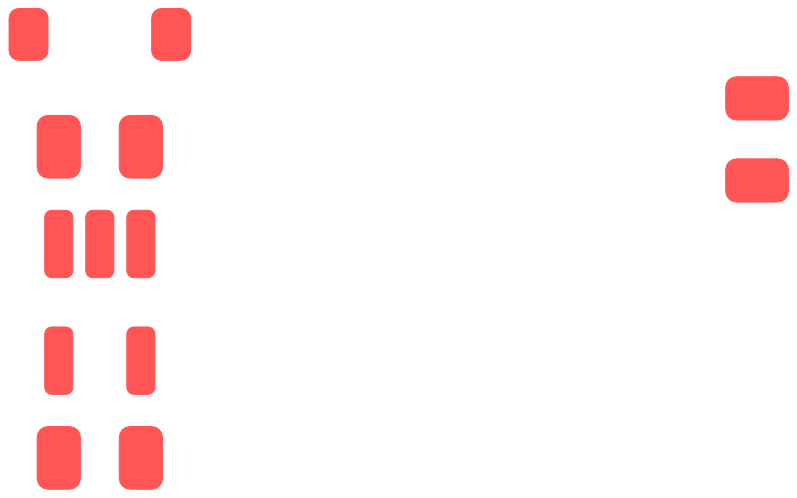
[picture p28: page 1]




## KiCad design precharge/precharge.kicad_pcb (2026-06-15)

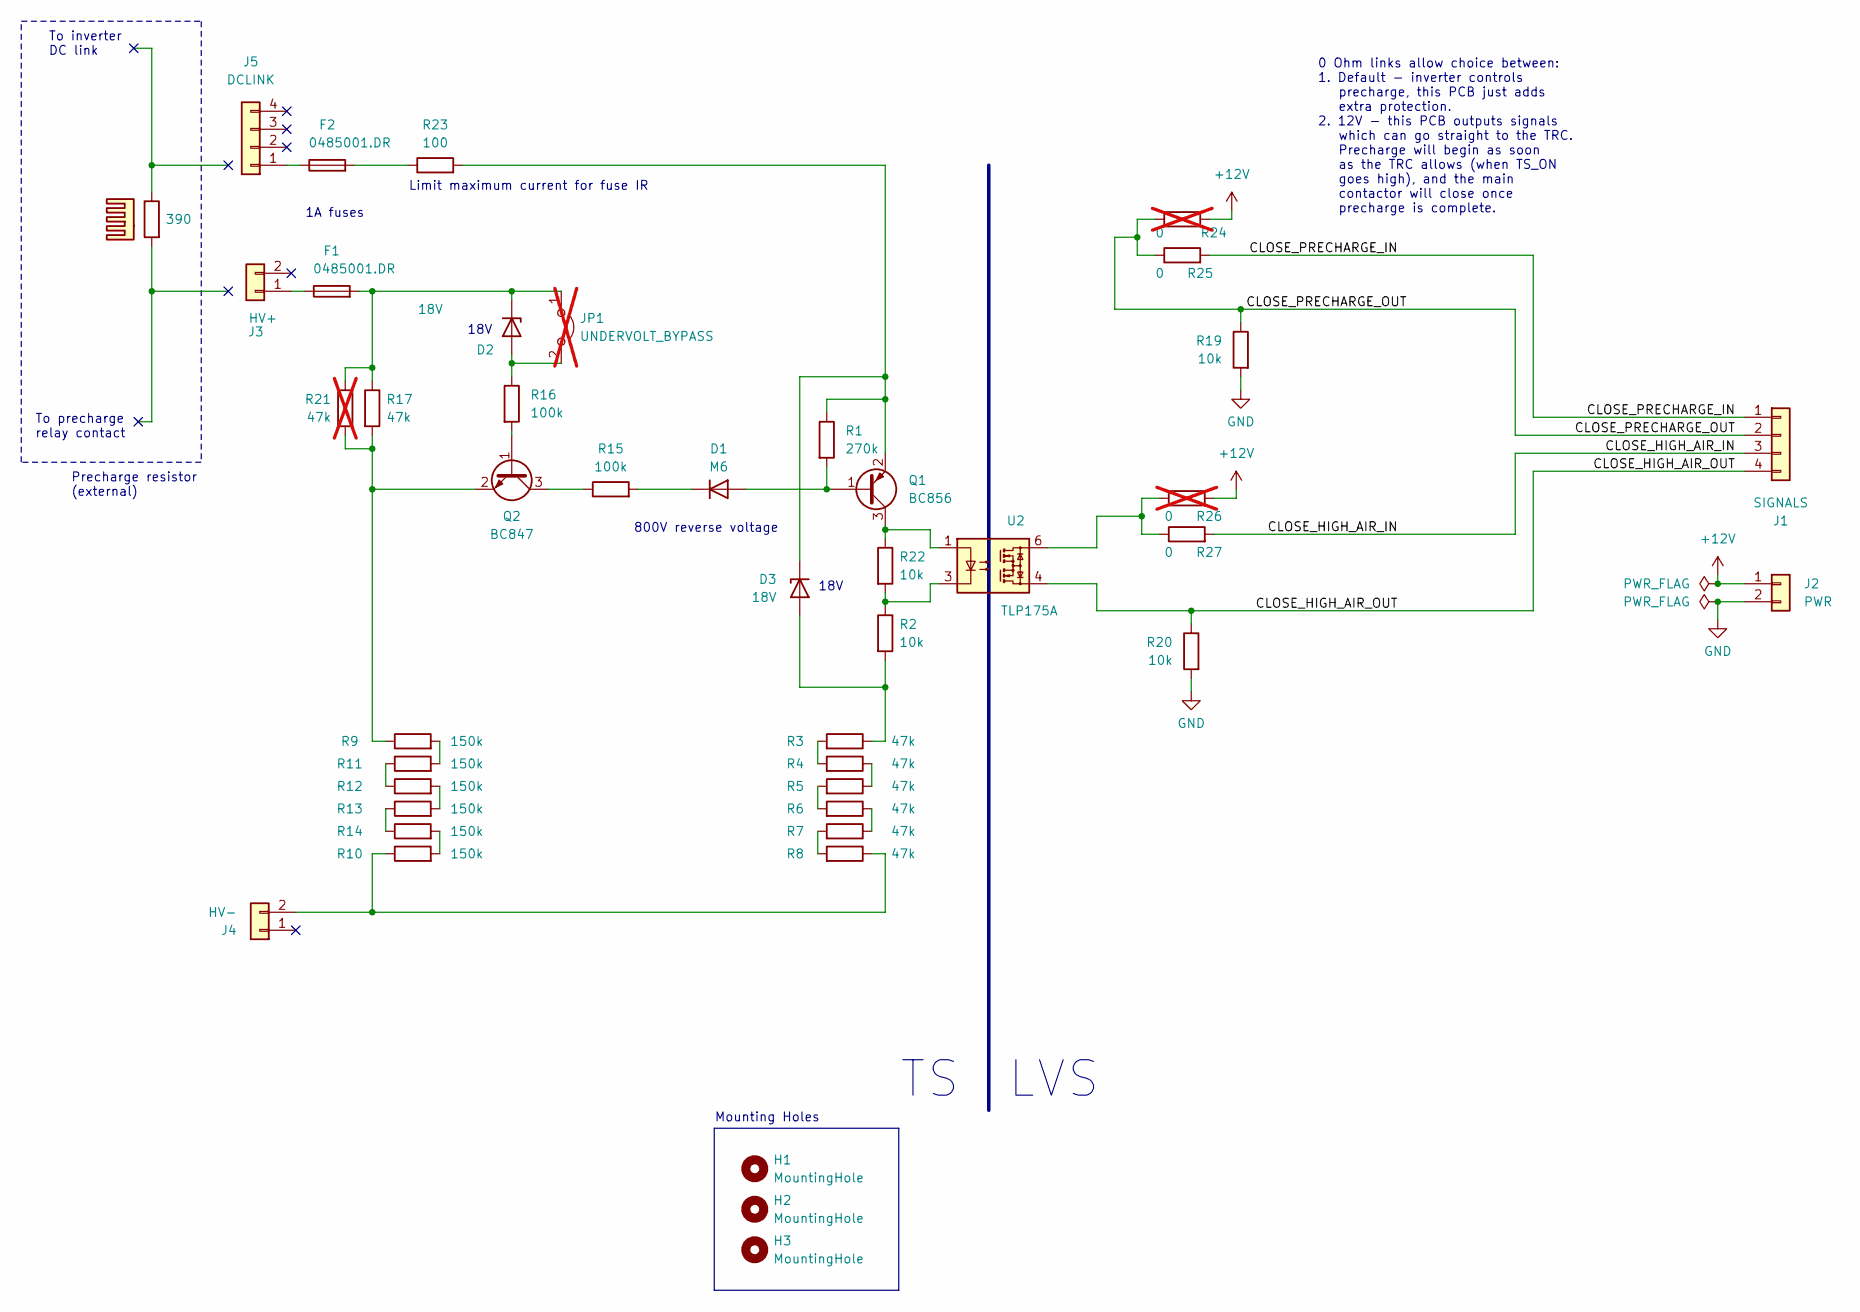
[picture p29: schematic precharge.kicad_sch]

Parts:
D1: M6; D_SMA_Handsoldering; MPN M6
D2, D3: 18V; D_SOD-123; MPN MMSZ5248B
F1, F2: 0485001.DR; Littelfuse-0485; MPN 0ACJ-1000-TE
H1, H2, H3: MountingHole; MountingHole_4.3mm_M4
HS1: Heatsink
J1: SIGNALS; Molex_Micro-Fit_3.0_43045-0412_2x02_P3.00mm_Vertical; MPN 43045-0412
J2: PWR; Molex_Micro-Fit_3.0_43045-0212_2x01_P3.00mm_Vertical; MPN 43045-0212
J3: HV+; Molex_Micro-Fit_3.0_43045-0212_2x01_P3.00mm_Vertical; MPN 43045-0412
J4: HV-; Molex_Micro-Fit_3.0_43045-0212_2x01_P3.00mm_Vertical; MPN 43045-0412
J5: DCLINK; Molex_Micro-Fit_3.0_43045-0412_2x02_P3.00mm_Vertical; MPN 43045-0412
JP1: UNDERVOLT_BYPASS; PinHeader_1x02_P2.54mm_Vertical; not fitted
Q1: BC856; SOT-23; MPN BC856A,215
Q2: BC847; SOT-23; MPN BC847A,215
R1: 270k; R_0805_2012Metric_Pad1.20x1.40mm_HandSolder; MPN AC0805FR-07270KL
R2, R19, R20, R22: 10k; R_0805_2012Metric_Pad1.20x1.40mm_HandSolder; MPN RT0603FRE1310KL
R3, R4, R5, R6, R7, R8: 47k; R_2512_6332Metric_Pad1.40x3.35mm_HandSolder; MPN RC2512FK-0747KL
R9, R10, R11, R12, R13, R14: 150k; R_0805_2012Metric_Pad1.20x1.40mm_HandSolder; MPN WR08X1503FTL
R15, R16: 100k; R_0805_2012Metric_Pad1.20x1.40mm_HandSolder; MPN RK73H2ATTDD1003F
R17: 47k; R_0805_2012Metric_Pad1.20x1.40mm_HandSolder; MPN AC0805FR-1347KL
R18: 390
R21: 47k; R_0805_2012Metric_Pad1.20x1.40mm_HandSolder; not fitted
R23: 100; R_0805_2012Metric_Pad1.20x1.40mm_HandSolder; MPN RC0805FR-13100RL
R24, R26: 0; R_0805_2012Metric_Pad1.20x1.40mm_HandSolder; not fitted
R25, R27: 0; R_0805_2012Metric_Pad1.20x1.40mm_HandSolder; MPN RC0805JR-130RL
U2: TLP175A; MFSOP6-4_4.4x3.6mm_P1.27mm; MPN TLP175A(TPLE

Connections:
+12V: J2.1, R24.2, R26.2
/CLOSE_HIGH_AIR_IN: J1.3, R27.2
/CLOSE_HIGH_AIR_OUT: J1.4, R20.1, U2.4
/CLOSE_PRECHARGE_IN: J1.1, R25.2
/CLOSE_PRECHARGE_OUT: J1.2, R19.1, R24.1, R25.1
GND: J2.2, R19.2, R20.2
unnamed: D1.2 (A), Q1.1 (B), R1.2
unnamed: D1.1 (K), R15.2
unnamed: D2.2 (A), JP1.2 (B), R16.1
unnamed: D2.1 (K), F1.2, JP1.1 (A), R17.1, R21.1
unnamed: D3.2 (A), R2.2, R3.1
unnamed: D3.1 (K), Q1.2 (E), R1.1, R23.2
unnamed: F2.2, R23.1
unnamed: F1.1, J3.1
unnamed: J4.2, R8.1, R10.1
unnamed: F2.1, J5.1
unnamed: Q1.3 (C), R22.1, U2.1
unnamed: Q2.1 (B), R16.2
unnamed: Q2.3 (C), R15.1
unnamed: Q2.2 (E), R9.1, R17.2, R21.2
unnamed: R2.1, R22.2, U2.3
unnamed: R3.2, R4.2
unnamed: R4.1, R5.1
unnamed: R5.2, R6.2
unnamed: R6.1, R7.1
unnamed: R7.2, R8.2
unnamed: R10.2, R14.2
unnamed: R11.1, R12.1
unnamed: R9.2, R11.2
unnamed: R12.2, R13.2
unnamed: R13.1, R14.1
unnamed: R26.1, R27.1, U2.6

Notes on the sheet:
18V
0 Ohm links allow choice between: 1. Default - inverter controls precharge, this PCB just adds extra protection. 2. 12V - this PCB outputs signals which can go straight to the TRC. Precharge will begin as soon as the TRC allows (when TS_ON goes high), and the main contactor will close once precharg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
To precharge relay contact
LVS
Mounting Holes
To inverter DC link
Precharge resistor (external)
Limit maximum current for fuse IR
800V reverse voltage
1A fuses

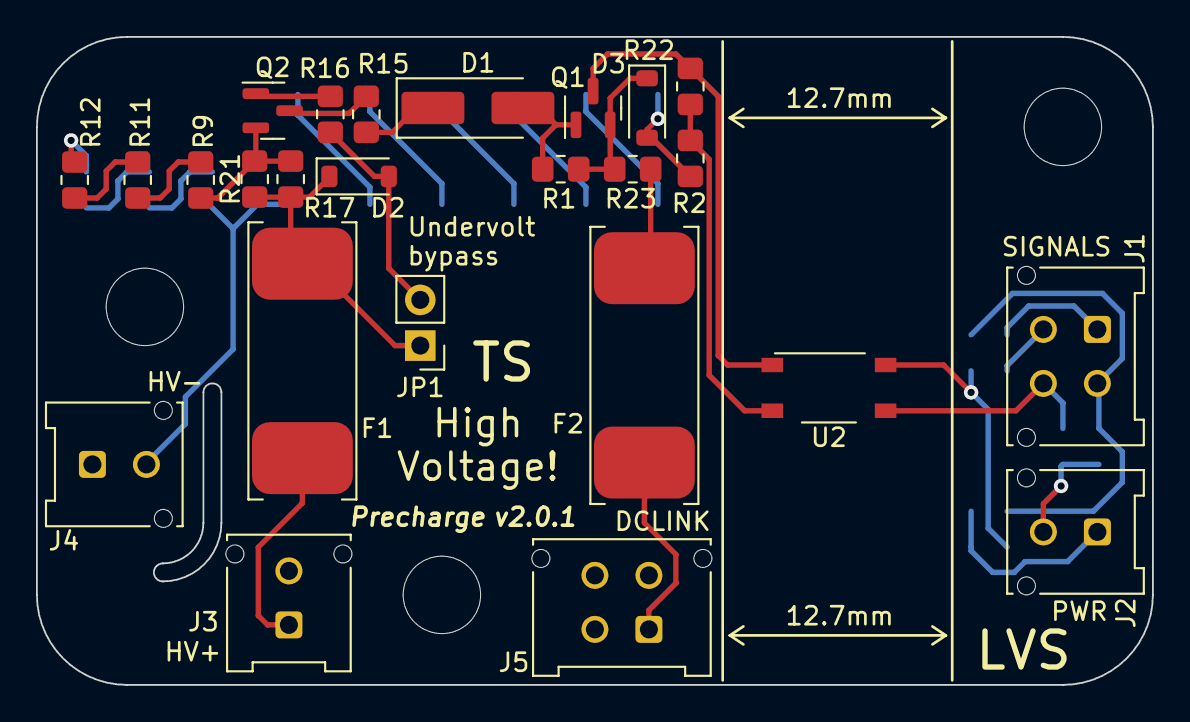
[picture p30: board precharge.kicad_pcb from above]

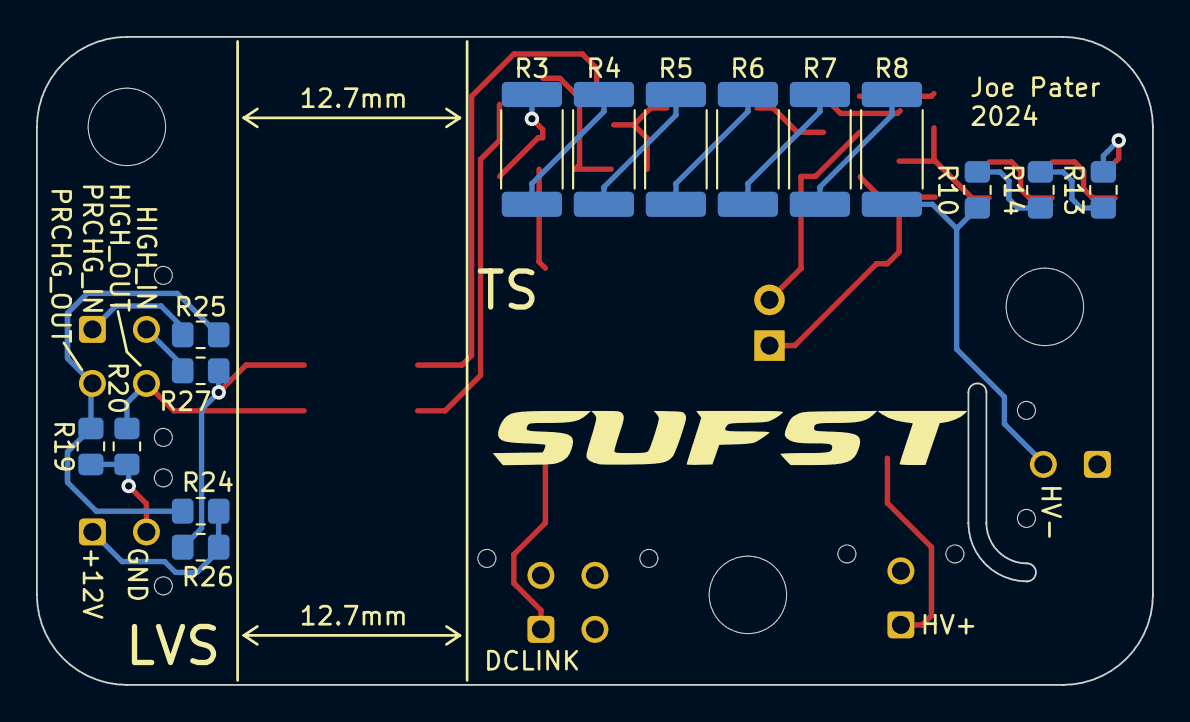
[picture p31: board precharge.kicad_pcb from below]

Board: 2 copper layers, 62.0 x 36.0 mm, 43 parts (15 on the bottom side), 32 nets.

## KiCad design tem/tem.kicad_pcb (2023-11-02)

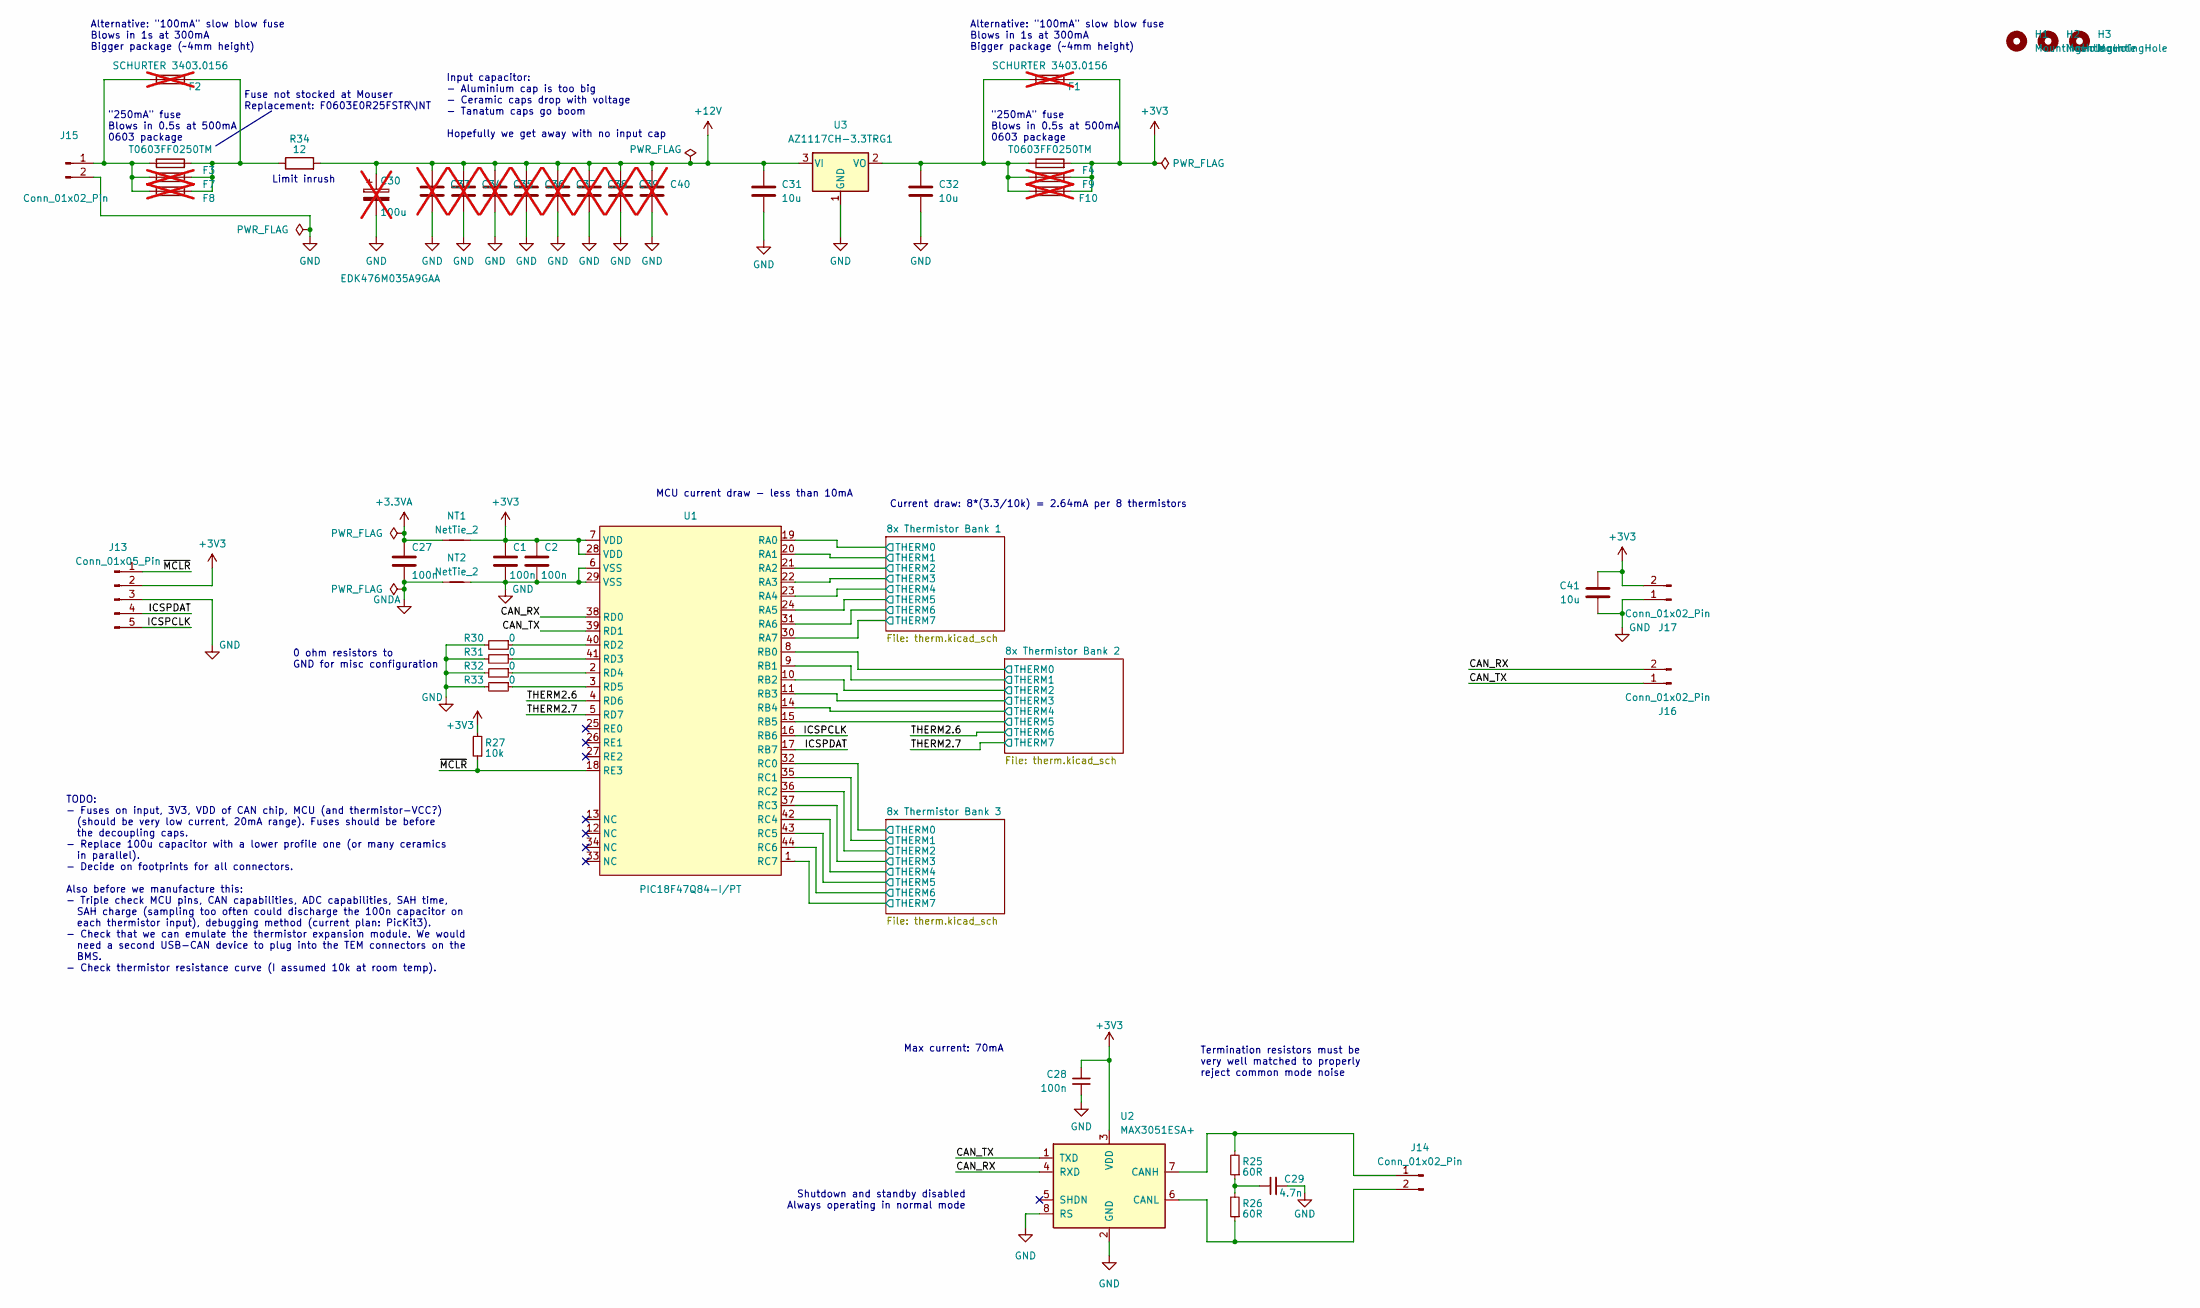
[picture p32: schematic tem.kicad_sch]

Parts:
C1, C2, C27, C28: 100n; C_0805_2012Metric_Pad1.18x1.45mm_HandSolder
C29: 4.7n; C_0805_2012Metric_Pad1.18x1.45mm_HandSolder
C30: 100u; CP_Elec_6.3x5.4; Part EDK476M035A9GAA; not fitted
C31, C32, C41: 10u; C_0805_2012Metric_Pad1.18x1.45mm_HandSolder
C33, C34, C35, C36, C37, C38, C39, C40: C_1206_3216Metric_Pad1.33x1.80mm_HandSolder; not fitted
F1, F2: SCHURTER 3403.0156; Fuse_Schurter_UMT250; not fitted
F3, F4: T0603FF0250TM; Fuse_0603_1608Metric_Pad1.05x0.95mm_HandSolder
F7, F8, F9, F10: T0603FF0250TM; Fuse_0603_1608Metric_Pad1.05x0.95mm_HandSolder; not fitted
H1, H2, H3: MountingHole; MountingHole_4.3mm_M4
J13: Conn_01x05_Pin; Conn5_SMD
J14, J15, J16, J17: Conn_01x02_Pin; Conn2_SMD
NT1, NT2: NetTie_2; R_0805_2012Metric_Pad1.20x1.40mm_HandSolder
R25, R26: 60R; R_0805_2012Metric_Pad1.20x1.40mm_HandSolder
R27: 10k; R_0805_2012Metric_Pad1.20x1.40mm_HandSolder
R30, R31, R32, R33: 0; R_0805_2012Metric_Pad1.20x1.40mm_HandSolder
R34: 12; R_0805_2012Metric_Pad1.20x1.40mm_HandSolder
U1: PIC18F47Q84-I/PT; TQFP-44_10x10mm_P0.8mm
U2: MAX3051ESA+; SOIC-8_3.9x4.9mm_P1.27mm
U3: AZ1117CH-3.3TRG1; SOT-223-3_TabPin2

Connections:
+3.3VA: C27.1, NT1.1; also elsewhere on the board
+3V3: C1.1, C2.1, C28.2, C41.1, F1.2, F4.2, F9.2, F10.2, J13.2, J17.2, NT1.2, R27.2, U1.7 (VDD), U1.28 (VDD), U2.3 (VDD)
+12V: C30.1, C31.1, C33.1, C34.1, C35.1, C36.1, C37.1, C38.1, C39.1, C40.1, R34.2, U3.3 (VI)
/8x Thermistor Bank 1/THERM0: U1.19 (RA0); also elsewhere on the board
/8x Thermistor Bank 1/THERM1: U1.20 (RA1); also elsewhere on the board
/8x Thermistor Bank 1/THERM2: U1.21 (RA2); also elsewhere on the board
/8x Thermistor Bank 1/THERM3: U1.22 (RA3); also elsewhere on the board
/8x Thermistor Bank 1/THERM4: U1.23 (RA4); also elsewhere on the board
/8x Thermistor Bank 1/THERM5: U1.24 (RA5); also elsewhere on the board
/8x Thermistor Bank 1/THERM6: U1.31 (RA6); also elsewhere on the board
/8x Thermistor Bank 1/THERM7: U1.30 (RA7); also elsewhere on the board
/8x Thermistor Bank 2/THERM0: U1.8 (RB0); also elsewhere on the board
/8x Thermistor Bank 2/THERM1: U1.9 (RB1); also elsewhere on the board
/8x Thermistor Bank 2/THERM2: U1.10 (RB2); also elsewhere on the board
/8x Thermistor Bank 2/THERM3: U1.11 (RB3); also elsewhere on the board
/8x Thermistor Bank 2/THERM4: U1.14 (RB4); also elsewhere on the board
/8x Thermistor Bank 2/THERM5: U1.15 (RB5); also elsewhere on the board
/8x Thermistor Bank 3/THERM0: U1.32 (RC0); also elsewhere on the board
/8x Thermistor Bank 3/THERM1: U1.35 (RC1); also elsewhere on the board
/8x Thermistor Bank 3/THERM2: U1.36 (RC2); also elsewhere on the board
/8x Thermistor Bank 3/THERM3: U1.37 (RC3); also elsewhere on the board
/8x Thermistor Bank 3/THERM4: U1.42 (RC4); also elsewhere on the board
/8x Thermistor Bank 3/THERM5: U1.43 (RC5); also elsewhere on the board
/8x Thermistor Bank 3/THERM6: U1.44 (RC6); also elsewhere on the board
/8x Thermistor Bank 3/THERM7: U1.1 (RC7); also elsewhere on the board
/CAN_RX: J16.2, U1.38 (RD0), U2.4 (RXD)
/CAN_TX: J16.1, U1.39 (RD1), U2.1 (TXD)
/ICSPCLK: J13.5, U1.16 (RB6)
/ICSPDAT: J13.4, U1.17 (RB7)
/THERM2.6: U1.4 (RD6); also elsewhere on the board
/THERM2.7: U1.5 (RD7); also elsewhere on the board
/~MCLR: J13.1, R27.1, U1.18 (RE3)
GND: C1.2, C2.2, C28.1, C29.2, C30.2, C31.2, C32.2, C33.2, C34.2, C35.2, C36.2, C37.2, C38.2, C39.2, C40.2, C41.2, J13.3, J15.2, J17.1, NT2.2, R30.2, R31.2, R32.2, R33.2, U1.6 (VSS), U1.29 (VSS), U2.2 (GND), U2.8 (RS), U3.1 (GND)
GNDA: C27.2, NT2.1; also elsewhere on the board
unnamed: C29.1, R25.1, R26.2
unnamed: F2.2, F3.2, F7.2, F8.2, R34.1
unnamed: J14.1, R25.2, U2.7 (CANH)
unnamed: J14.2, R26.1, U2.6 (CANL)
unnamed: F2.1, F3.1, F7.1, F8.1, J15.1
unnamed: R30.1, U1.40 (RD2)
unnamed: R31.1, U1.41 (RD3)
unnamed: R32.1, U1.2 (RD4)
unnamed: R33.1, U1.3 (RD5)
unnamed: C32.1, F1.1, F4.1, F9.1, F10.1, U3.2 (VO)

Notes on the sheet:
Alternative: "100mA" slow blow fuse Blows in 1s at 300mA Bigger package (~4mm height)
MCU current draw - less than 10mA
Max current: 70mA
Shutdown and standby disabled Always operating in normal mode
"250mA" fuse Blows in 0.5s at 500mA 0603 package
Input capacitor: - Aluminium cap is too big - Ceramic caps drop with voltage - Tanatum caps go boom Hopefully we get away with no input cap
Current draw: 8*(3.3/10k) = 2.64mA per 8 thermistors
0 ohm resistors to GND for misc configuration
TODO: - Fuses on input, 3V3, VDD of CAN chip, MCU (and thermistor-VCC?) (should be very low current, 20mA range). Fuses should be before the decoupling caps. - Replace 100u capacitor with a lower profile one (or many ceramics in parallel). - Decide on footprints for all connectors. Also before we m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
Fuse not stocked at Mouser Replacement: F0603E0R25FSTR\INT
Limit inrush
Termination resistors must be very well matched to properly reject common mode noise

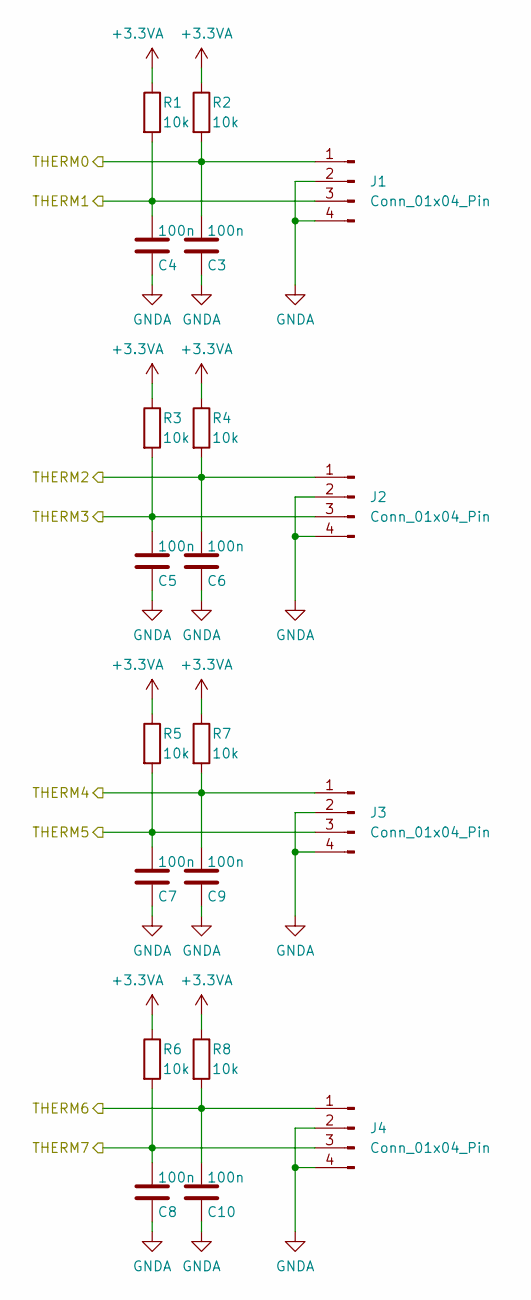
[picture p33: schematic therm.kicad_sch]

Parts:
C3, C4, C5, C6, C7, C8, C9, C10: 100n; C_0805_2012Metric_Pad1.18x1.45mm_HandSolder
J1, J2, J3, J4: Conn_01x04_Pin; Thermistor_x2
R1, R2, R3, R4, R5, R6, R7, R8: 10k; R_0805_2012Metric_Pad1.20x1.40mm_HandSolder

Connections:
+3.3VA: R1.1, R2.1, R3.1, R4.1, R5.1, R6.1, R7.1, R8.1; also elsewhere on the board
/8x Thermistor Bank 1/THERM0: C3.1, J1.1, R2.2; also elsewhere on the board
/8x Thermistor Bank 1/THERM1: C4.1, J1.3, R1.2; also elsewhere on the board
/8x Thermistor Bank 1/THERM2: C6.1, J2.1, R4.2; also elsewhere on the board
/8x Thermistor Bank 1/THERM3: C5.1, J2.3, R3.2; also elsewhere on the board
/8x Thermistor Bank 1/THERM4: C9.1, J3.1, R7.2; also elsewhere on the board
/8x Thermistor Bank 1/THERM5: C7.1, J3.3, R5.2; also elsewhere on the board
/8x Thermistor Bank 1/THERM6: C10.1, J4.1, R8.2; also elsewhere on the board
/8x Thermistor Bank 1/THERM7: C8.1, J4.3, R6.2; also elsewhere on the board
GNDA: C3.2, C4.2, C5.2, C6.2, C7.2, C8.2, C9.2, C10.2, J1.2, J1.4, J2.2, J2.4, J3.2, J3.4, J4.2, J4.4; also elsewhere on the board

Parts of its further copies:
C11, C12, C13, C14, C15, C16, C17, C18, C19, C20, C21, C22, C23, C24, C25, C26: 100n; C_0805_2012Metric_Pad1.18x1.45mm_HandSolder
J5, J6, J7, J8, J9, J10, J11, J12: Conn_01x04_Pin; Thermistor_x2
R9, R10, R11, R12, R13, R14, R15, R16, R17, R18, R19, R20, R21, R22, R23, R24: 10k; R_0805_2012Metric_Pad1.20x1.40mm_HandSolder

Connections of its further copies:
+3.3VA: R9.1, R10.1, R11.1, R12.1, R13.1, R14.1, R15.1, R16.1, R17.1, R18.1, R19.1, R20.1, R21.1, R22.1, R23.1, R24.1; also elsewhere on the board
/8x Thermistor Bank 2/THERM0: C15.1, J5.1, R13.2; also elsewhere on the board
/8x Thermistor Bank 2/THERM1: C11.1, J5.3, R9.2; also elsewhere on the board
/8x Thermistor Bank 2/THERM2: C16.1, J6.1, R14.2; also elsewhere on the board
/8x Thermistor Bank 2/THERM3: C12.1, J6.3, R10.2; also elsewhere on the board
/8x Thermistor Bank 2/THERM4: C17.1, J7.1, R15.2; also elsewhere on the board
/8x Thermistor Bank 2/THERM5: C13.1, J7.3, R11.2; also elsewhere on the board
/8x Thermistor Bank 3/THERM0: C23.1, J9.1, R21.2; also elsewhere on the board
/8x Thermistor Bank 3/THERM1: C19.1, J9.3, R17.2; also elsewhere on the board
/8x Thermistor Bank 3/THERM2: C24.1, J10.1, R22.2; also elsewhere on the board
/8x Thermistor Bank 3/THERM3: C20.1, J10.3, R18.2; also elsewhere on the board
/8x Thermistor Bank 3/THERM4: C25.1, J11.1, R23.2; also elsewhere on the board
/8x Thermistor Bank 3/THERM5: C21.1, J11.3, R19.2; also elsewhere on the board
/8x Thermistor Bank 3/THERM6: C26.1, J12.1, R24.2; also elsewhere on the board
/8x Thermistor Bank 3/THERM7: C22.1, J12.3, R20.2; also elsewhere on the board
/THERM2.6: C18.1, J8.1, R16.2; also elsewhere on the board
/THERM2.7: C14.1, J8.3, R12.2; also elsewhere on the board
GNDA: C11.2, C12.2, C13.2, C14.2, C15.2, C16.2, C17.2, C18.2, C19.2, C20.2, C21.2, C22.2, C23.2, C24.2, C25.2, C26.2, J5.2, J5.4, J6.2, J6.4, J7.2, J7.4, J8.2, J8.4, J9.2, J9.4, J10.2, J10.4, J11.2, J11.4, J12.2, J12.4; also elsewhere on the board

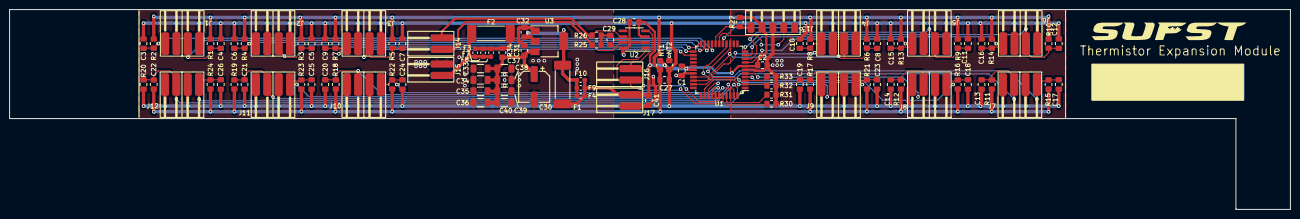
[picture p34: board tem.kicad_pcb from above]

Board: 2 copper layers, 282.0 x 44.0 mm, 103 parts (0 on the bottom side), 44 nets.

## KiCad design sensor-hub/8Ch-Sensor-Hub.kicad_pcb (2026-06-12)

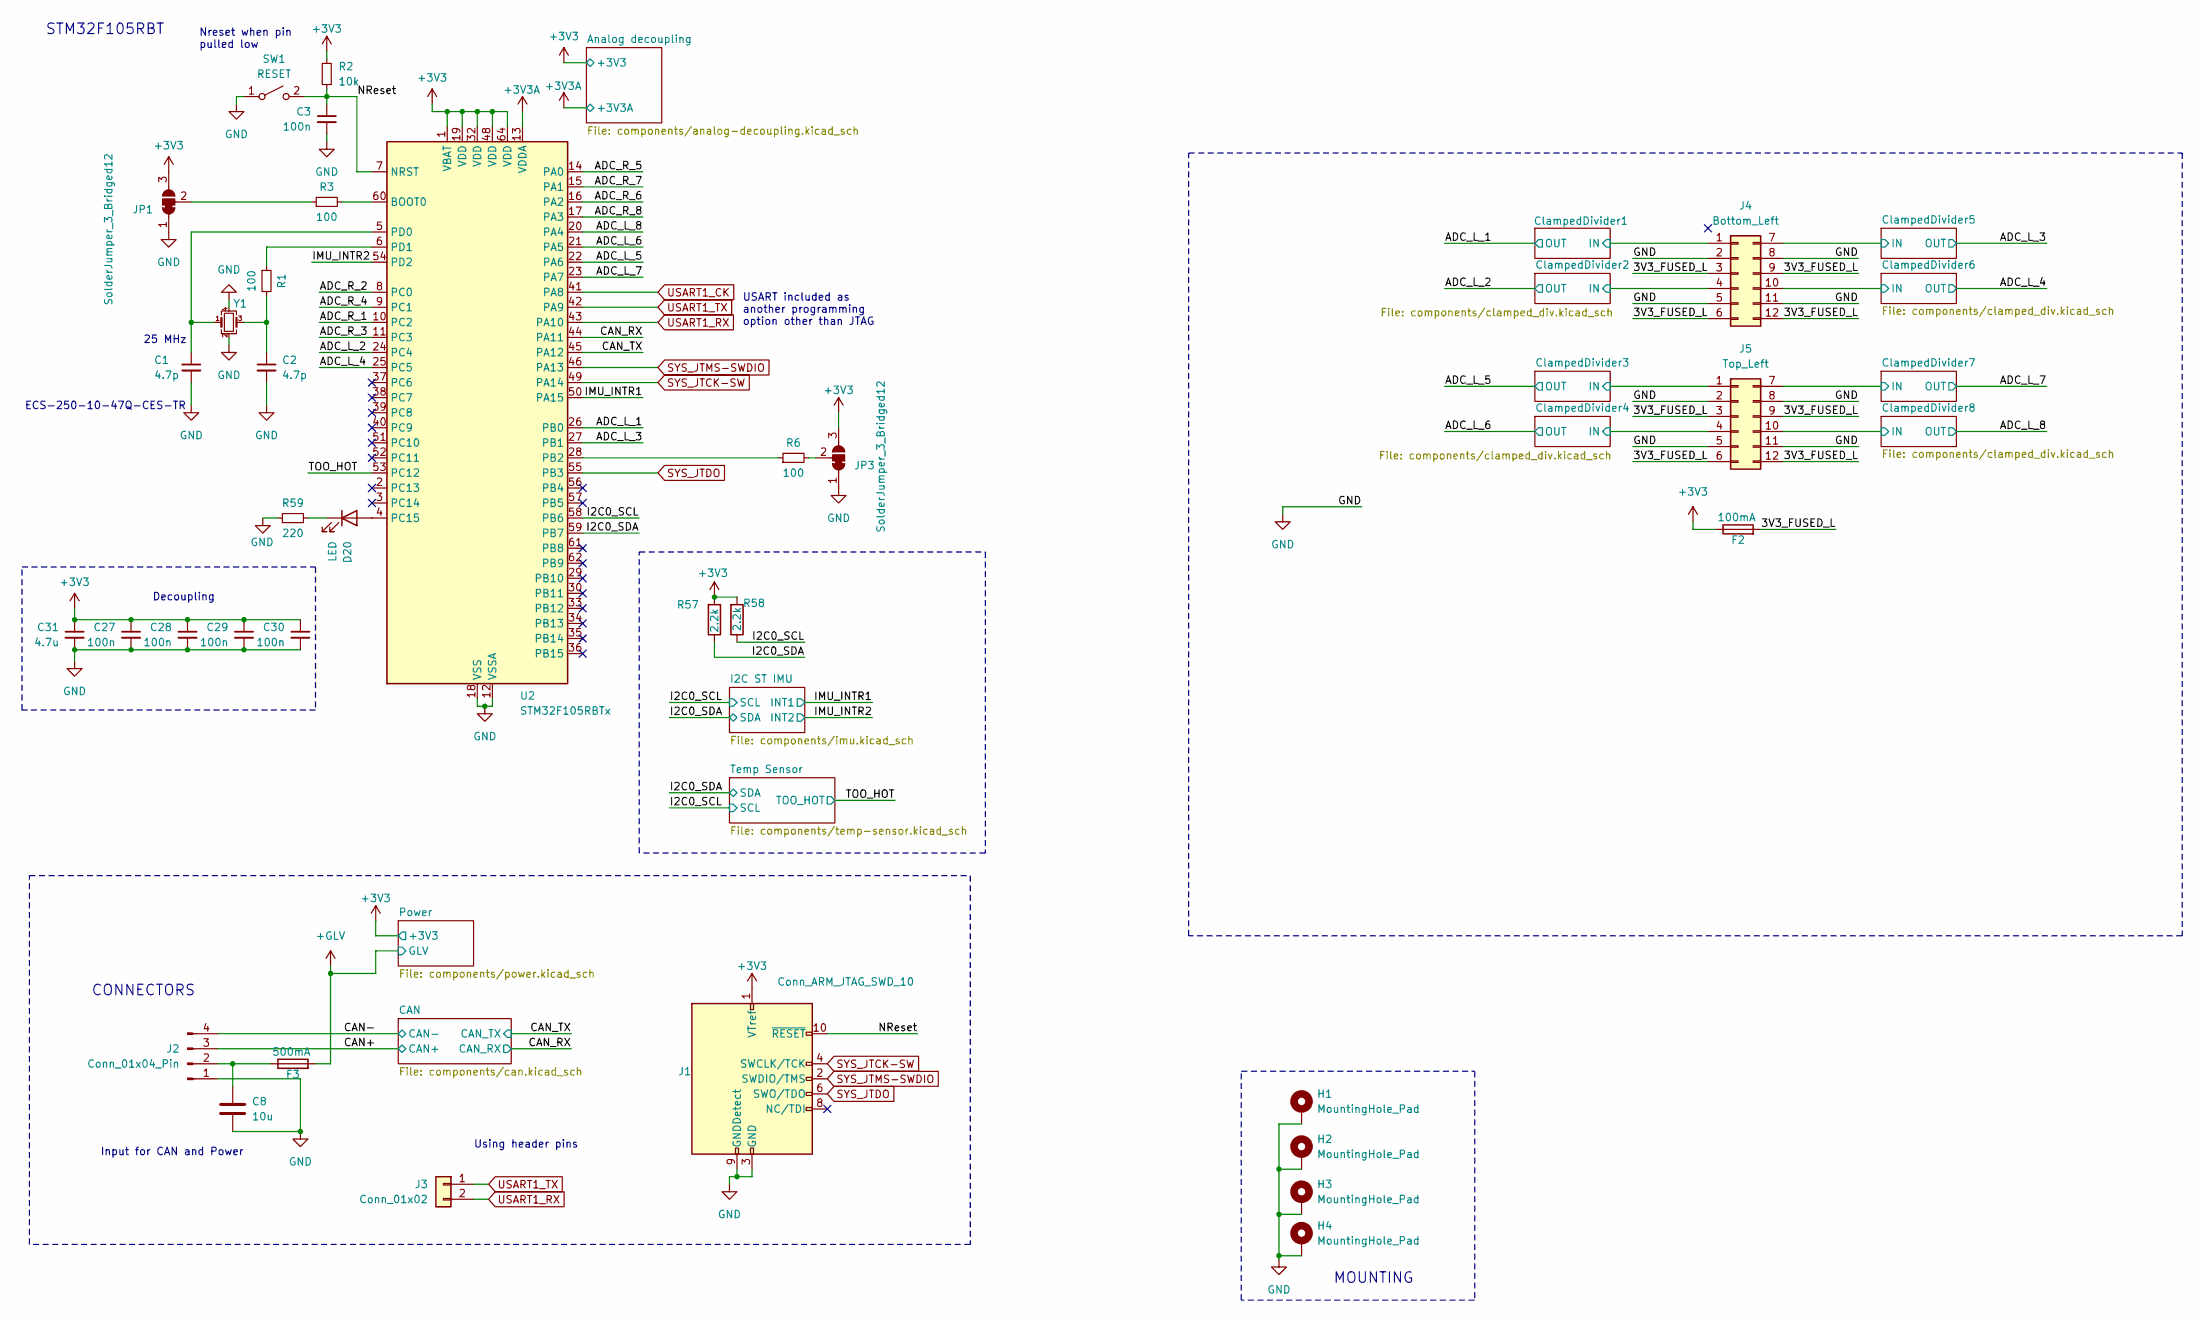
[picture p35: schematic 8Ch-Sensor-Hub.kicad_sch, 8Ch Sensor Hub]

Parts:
C1, C2: 4.7p; C_0603_1608Metric_Pad1.08x0.95mm_HandSolder
C3, C27, C28, C29, C30: 100n; C_0603_1608Metric_Pad1.08x0.95mm_HandSolder
C8: 10u; C_0603_1608Metric_Pad1.08x0.95mm_HandSolder
C31: 4.7u; C_0603_1608Metric_Pad1.08x0.95mm_HandSolder
D20: LED; LED_0603_1608Metric_Pad1.05x0.95mm_HandSolder
F2: 100mA; Fuse_0603_1608Metric_Pad1.05x0.95mm_HandSolder
F3: 500mA; Fuse_0603_1608Metric_Pad1.05x0.95mm_HandSolder
H1, H2, H3, H4: MountingHole_Pad; MountingHole_3.2mm_M3_Pad_Via
J1: Conn_ARM_JTAG_SWD_10; SHF10501LDSMLC; MPN SHF-105-01-L-D-SM-LC
J2: Conn_01x04_Pin; Molex_Micro-Fit_3.0_43045-0400_2x02_P3.00mm_Horizontal
J3: Conn_01x02; PinHeader_1x02_P2.54mm_Vertical
J4: Bottom_Left; Molex_Micro-Fit_3.0_43045-1200_2x06_P3.00mm_Horizontal
J5: Top_Left; Molex_Micro-Fit_3.0_43045-1200_2x06_P3.00mm_Horizontal
JP1, JP3: SolderJumper_3_Bridged12; SolderJumper-3_P1.3mm_Bridged12_RoundedPad1.0x1.5mm
R1, R3, R6: 100; R_0603_1608Metric_Pad0.98x0.95mm_HandSolder
R2: 10k; R_0603_1608Metric_Pad0.98x0.95mm_HandSolder
R57, R58: 2.2k; R_0603_1608Metric_Pad0.98x0.95mm_HandSolder; Mouser Order Number 603-RC0402FR-072K2L
R59: 220; R_0603_1608Metric_Pad0.98x0.95mm_HandSolder
SW1: RESET; SW_Push_1P1T_NO_CK_KMR2; MPN KMR221NG LFS
U2: STM32F105RBTx; LQFP-64_10x10mm_P0.5mm
Y1: ECS-250-10-47Q-CES-TR; Resonator_SMD_ECS_ECX-1247Q_1.6x1.2x0.3mm; MPN ECS-250-10-47Q-CES-TR

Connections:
+3V3: C27.1, C28.1, C29.1, C30.1, C31.1, F2.1, J1.1 (VTref), JP1.3 (B), JP3.3 (B), R2.2, R57.2, R58.2, U2.1 (VBAT), U2.19 (VDD), U2.32 (VDD), U2.48 (VDD), U2.64 (VDD); also elsewhere on the board
+3V3A: U2.13 (VDDA); also elsewhere on the board
+GLV: F3.2; also elsewhere on the board
/3V3_FUSED_L: F2.2, J4.3, J4.6, J4.9, J4.12, J5.3, J5.6, J5.9, J5.12
/ADC_L_1: U2.26 (PB0); also elsewhere on the board
/ADC_L_2: U2.24 (PC4); also elsewhere on the board
/ADC_L_3: U2.27 (PB1); also elsewhere on the board
/ADC_L_4: U2.25 (PC5); also elsewhere on the board
/ADC_L_5: U2.22 (PA6); also elsewhere on the board
/ADC_L_6: U2.21 (PA5); also elsewhere on the board
/ADC_L_7: U2.23 (PA7); also elsewhere on the board
/ADC_L_8: U2.20 (PA4); also elsewhere on the board
/ADC_R_1: U2.10 (PC2)
/ADC_R_2: U2.8 (PC0)
/ADC_R_3: U2.11 (PC3)
/ADC_R_4: U2.9 (PC1)
/ADC_R_5: U2.14 (PA0)
/ADC_R_6: U2.16 (PA2)
/ADC_R_7: U2.15 (PA1)
/ADC_R_8: U2.17 (PA3)
/CAN+: J2.3; also elsewhere on the board
/CAN-: J2.4; also elsewhere on the board
/CAN_RX: U2.44 (PA11); also elsewhere on the board
/CAN_TX: U2.45 (PA12); also elsewhere on the board
/ClampedDivider1/IN: J4.1; also elsewhere on the board
/ClampedDivider2/IN: J4.4; also elsewhere on the board
/ClampedDivider3/IN: J5.1; also elsewhere on the board
/ClampedDivider4/IN: J5.4; also elsewhere on the board
/ClampedDivider5/IN: J4.7; also elsewhere on the board
/ClampedDivider6/IN: J4.10; also elsewhere on the board
/ClampedDivider7/IN: J5.7; also elsewhere on the board
/ClampedDivider8/IN: J5.10; also elsewhere on the board
/I2C0_SCL: R58.1, U2.58 (PB6); also elsewhere on the board
/I2C0_SDA: R57.1, U2.59 (PB7); also elsewhere on the board
/IMU_INTR1: U2.50 (PA15); also elsewhere on the board
/IMU_INTR2: U2.54 (PD2); also elsewhere on the board
/NReset: C3.1, J1.10 (~RESET), R2.1, SW1.2 (B), U2.7 (NRST)
/TOO_HOT: U2.53 (PC12); also elsewhere on the board
GND: C1.2, C2.2, C3.2, C8.2, C27.2, C28.2, C29.2, C30.2, C31.2, H1.1, H2.1, H3.1, H4.1, J1.3 (GND), J1.5 (GND), J1.9 (GNDDetect), J2.1, J4.2, J4.5, J4.8, J4.11, J5.2, J5.5, J5.8, J5.11, JP1.1 (A), JP3.1 (A), R59.1, SW1.1 (A), U2.12 (VSSA), U2.18 (VSS), U2.31 (VSS), U2.47 (VSS), U2.63 (VSS), Y1.2, Y1.4; also elsewhere on the board
unnamed: C2.1, R1.2, Y1.3
unnamed: D20.2 (A), U2.4 (PC15)
unnamed: D20.1 (K), R59.2
unnamed: C8.1, F3.1, J2.2
unnamed: JP1.2 (C), R3.1
unnamed: JP3.2 (C), R6.2
unnamed: R3.2, U2.60 (BOOT0)
unnamed: R6.1, U2.28 (PB2)
unnamed: C1.1, U2.5 (PD0), Y1.1
unnamed: R1.1, U2.6 (PD1)
SYS_JTCK-SW: J1.4 (SWCLK/TCK), U2.49 (PA14)
SYS_JTDO: J1.6 (SWO/TDO), U2.55 (PB3)
SYS_JTMS-SWDIO: J1.2 (SWDIO/TMS), U2.46 (PA13)
USART1_CK: U2.41 (PA8)
USART1_RX: J3.2, U2.43 (PA10)
USART1_TX: J3.1, U2.42 (PA9)

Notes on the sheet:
25 MHz
STM32F105RBT
Input for CAN and Power
CONNECTORS
Nreset when pin pulled low
ECS-250-10-47Q-CES-TR
Decoupling
Using header pins
USART included as another programming option other than JTAG
MOUNTING

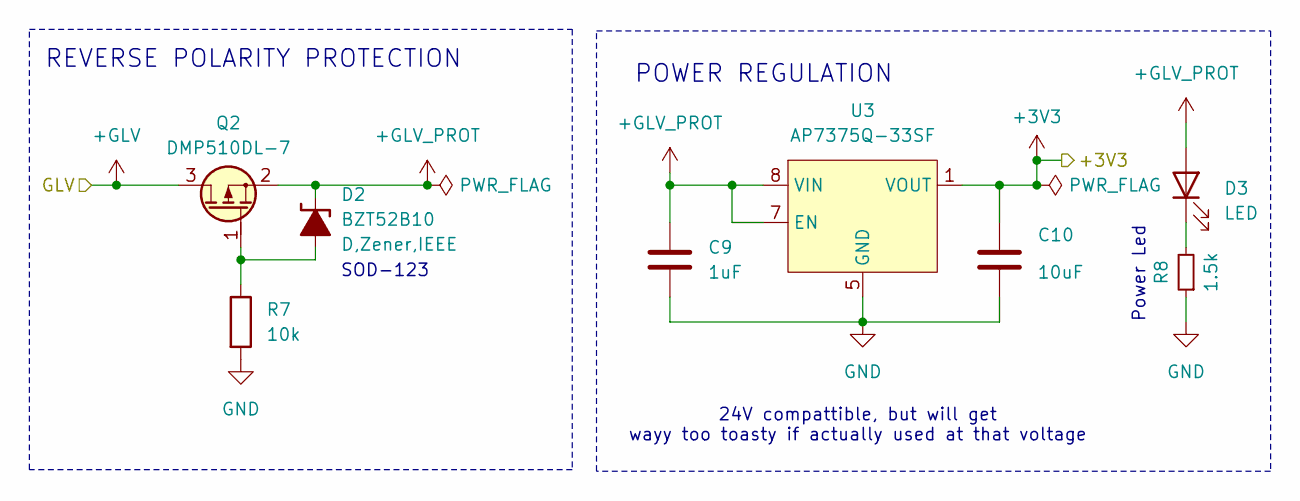
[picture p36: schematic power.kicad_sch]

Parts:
C9: 1uF; C_0603_1608Metric_Pad1.08x0.95mm_HandSolder
C10: 10uF; C_0603_1608Metric_Pad1.08x0.95mm_HandSolder
D2: BZT52B10; D_SOD-123; MPN BZT52B10
D3: LED; LED_0603_1608Metric_Pad1.05x0.95mm_HandSolder
Q2: DMP510DL-7; SOT-23
R7: 10k; R_0603_1608Metric_Pad0.98x0.95mm_HandSolder
R8: 1.5k; R_0603_1608Metric_Pad0.98x0.95mm_HandSolder
U3: AP7375Q-33SF; Diodes_SO-8EP

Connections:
+3V3: C10.1, U3.1 (VOUT); also elsewhere on the board
+GLV: Q2.3 (D); also elsewhere on the board
+GLV_PROT: C9.1, D2.1 (K-), D3.2 (A), Q2.2 (S), U3.7 (EN), U3.8 (VIN); also elsewhere on the board
GND: C9.2, C10.2, R7.2, R8.1, U3.2, U3.3, U3.4, U3.5 (GND), U3.6, U3.9 (EP); also elsewhere on the board
unnamed: D2.2 (A+), Q2.1 (G), R7.1
unnamed: D3.1 (K), R8.2

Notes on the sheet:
24V compattible, but will get wayy too toasty if actually used at that voltage
Power Led
POWER REGULATION
SOD-123
REVERSE POLARITY PROTECTION

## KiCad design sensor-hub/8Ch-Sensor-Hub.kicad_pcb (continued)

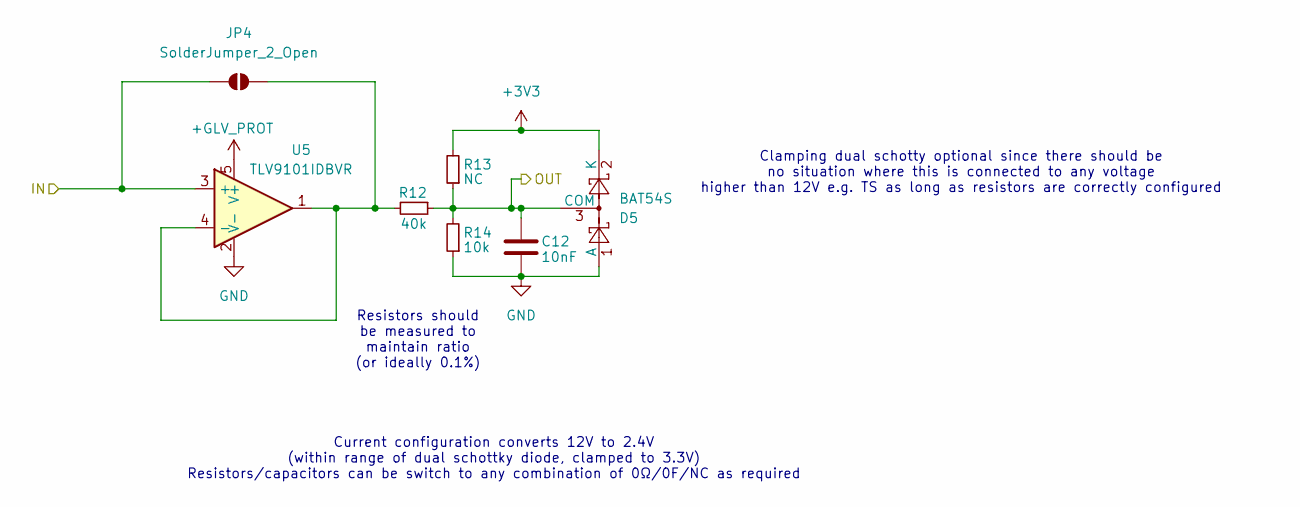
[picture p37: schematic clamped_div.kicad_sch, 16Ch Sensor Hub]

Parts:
C12: 10nF; C_0603_1608Metric_Pad1.08x0.95mm_HandSolder
D5: BAT54S; SOT-23
JP4: SolderJumper_2_Open; SolderJumper-2_P1.3mm_Open_RoundedPad1.0x1.5mm
R12: 40k; R_0603_1608Metric_Pad0.98x0.95mm_HandSolder; Manufacturer_Part_Number CRCW080540K0FKEA; Mouser Part Number 71-CRCW080540K0FKEA
R13: NC; R_0603_1608Metric_Pad0.98x0.95mm_HandSolder; Manufacturer_Part_Number CRGH0805F12R; Mouser Part Number 279-CRGH0805F12R
R14: 10k; R_0603_1608Metric_Pad0.98x0.95mm_HandSolder; Manufacturer_Part_Number CRGH0805F12R; Mouser Part Number 279-CRGH0805F12R
U5: TLV9101IDBVR; SOT-23-5_HandSoldering

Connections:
+3V3: D5.2 (K), R13.2; also elsewhere on the board
+GLV_PROT: U5.5 (V+); also elsewhere on the board
/ADC_L_4: C12.1, D5.3 (COM), R12.1, R13.1, R14.2; also elsewhere on the board
/ClampedDivider6/IN: JP4.1 (A), U5.3 (+); also elsewhere on the board
GND: C12.2, D5.1 (A), R14.1, U5.2 (V-); also elsewhere on the board
unnamed: JP4.2 (B), R12.2, U5.1, U5.4 (-)

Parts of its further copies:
C11, C13, C14, C15, C16, C17, C18: 10nF; C_0603_1608Metric_Pad1.08x0.95mm_HandSolder
D4, D6, D7, D8, D9, D10, D11: BAT54S; SOT-23
JP5, JP6, JP7, JP8, JP9, JP10, JP11: SolderJumper_2_Open; SolderJumper-2_P1.3mm_Open_RoundedPad1.0x1.5mm
R9, R15, R18, R21, R24, R27, R30: 40k; R_0603_1608Metric_Pad0.98x0.95mm_HandSolder; Manufacturer_Part_Number CRCW080540K0FKEA; Mouser Part Number 71-CRCW080540K0FKEA
R10, R16, R19, R22, R25, R28, R31: NC; R_0603_1608Metric_Pad0.98x0.95mm_HandSolder; Manufacturer_Part_Number CRGH0805F12R; Mouser Part Number 279-CRGH0805F12R
R11, R17, R20, R23, R26, R29, R32: 10k; R_0603_1608Metric_Pad0.98x0.95mm_HandSolder; Manufacturer_Part_Number CRGH0805F12R; Mouser Part Number 279-CRGH0805F12R
U4, U6, U7, U8, U9, U10, U11: TLV9101IDBVR; SOT-23-5_HandSoldering

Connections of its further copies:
+3V3: D4.2 (K), D6.2 (K), D7.2 (K), D8.2 (K), D9.2 (K), D10.2 (K), D11.2 (K), R10.2, R16.2, R19.2, R22.2, R25.2, R28.2, R31.2; also elsewhere on the board
+GLV_PROT: U4.5 (V+), U6.5 (V+), U7.5 (V+), U8.5 (V+), U9.5 (V+), U10.5 (V+), U11.5 (V+); also elsewhere on the board
/ADC_L_1: C15.1, D8.3 (COM), R21.1, R22.1, R23.2; also elsewhere on the board
/ADC_L_2: C16.1, D9.3 (COM), R24.1, R25.1, R26.2; also elsewhere on the board
/ADC_L_3: C11.1, D4.3 (COM), R9.1, R10.1, R11.2; also elsewhere on the board
/ADC_L_5: C17.1, D10.3 (COM), R27.1, R28.1, R29.2; also elsewhere on the board
/ADC_L_6: C18.1, D11.3 (COM), R30.1, R31.1, R32.2; also elsewhere on the board
/ADC_L_7: C13.1, D6.3 (COM), R15.1, R16.1, R17.2; also elsewhere on the board
/ADC_L_8: C14.1, D7.3 (COM), R18.1, R19.1, R20.2; also elsewhere on the board
/ClampedDivider1/IN: JP8.1 (A), U8.3 (+); also elsewhere on the board
/ClampedDivider2/IN: JP9.1 (A), U9.3 (+); also elsewhere on the board
/ClampedDivider3/IN: JP10.1 (A), U10.3 (+); also elsewhere on the board
/ClampedDivider4/IN: JP11.1 (A), U11.3 (+); also elsewhere on the board
/ClampedDivider5/IN: JP5.1 (A), U4.3 (+); also elsewhere on the board
/ClampedDivider7/IN: JP6.1 (A), U6.3 (+); also elsewhere on the board
/ClampedDivider8/IN: JP7.1 (A), U7.3 (+); also elsewhere on the board
GND: C11.2, C13.2, C14.2, C15.2, C16.2, C17.2, C18.2, D4.1 (A), D6.1 (A), D7.1 (A), D8.1 (A), D9.1 (A), D10.1 (A), D11.1 (A), R11.1, R17.1, R20.1, R23.1, R26.1, R29.1, R32.1, U4.2 (V-), U6.2 (V-), U7.2 (V-), U8.2 (V-), U9.2 (V-), U10.2 (V-), U11.2 (V-); also elsewhere on the board
unnamed: JP5.2 (B), R9.2, U4.1, U4.4 (-)
unnamed: JP6.2 (B), R15.2, U6.1, U6.4 (-)
unnamed: JP7.2 (B), R18.2, U7.1, U7.4 (-)
unnamed: JP8.2 (B), R21.2, U8.1, U8.4 (-)
unnamed: JP9.2 (B), R24.2, U9.1, U9.4 (-)
unnamed: JP10.2 (B), R27.2, U10.1, U10.4 (-)
unnamed: JP11.2 (B), R30.2, U11.1, U11.4 (-)

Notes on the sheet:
Current configuration converts 12V to 2.4V (within range of dual schottky diode, clamped to 3.3V) Resistors/capacitors can be switch to any combination of 0Ω/0F/NC as required
Clamping dual schotty optional since there should be no situation where this is connected to any voltage higher than 12V e.g. TS as long as resistors are correctly configured
Resistors should be measured to maintain ratio (or ideally 0.1%)

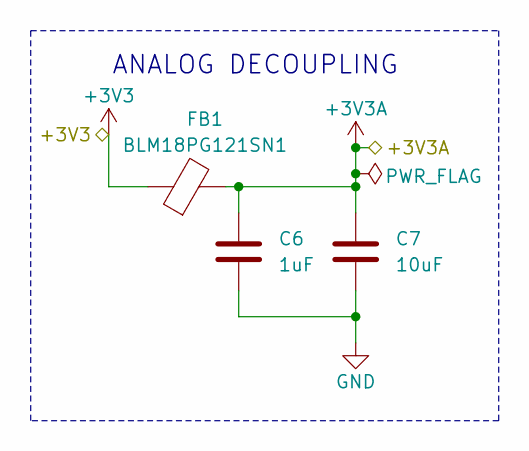
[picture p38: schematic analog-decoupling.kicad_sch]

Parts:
C6: 1uF; C_0603_1608Metric_Pad1.08x0.95mm_HandSolder
C7: 10uF; C_0603_1608Metric_Pad1.08x0.95mm_HandSolder
FB1: BLM18PG121SN1; L_0603_1608Metric_Pad1.05x0.95mm_HandSolder

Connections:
+3V3: FB1.1; also elsewhere on the board
+3V3A: C6.1, C7.1, FB1.2; also elsewhere on the board
GND: C6.2, C7.2; also elsewhere on the board

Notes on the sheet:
ANALOG DECOUPLING

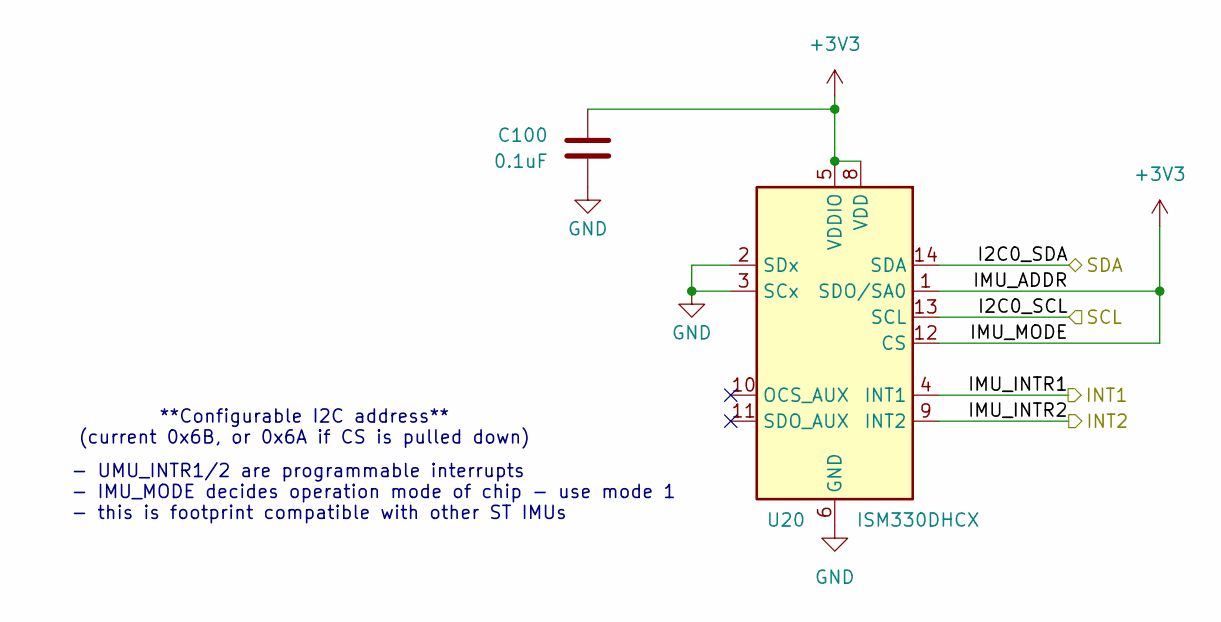
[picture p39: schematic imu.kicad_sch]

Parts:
C100: 0.1uF; C_0603_1608Metric_Pad1.08x0.95mm_HandSolder; Mouser Order Number 81-GRM155R62A104KE4J
U20: ISM330DHCX; LGA-14_3x2.5mm_P0.5mm_LayoutBorder3x4y; Mouser Order Number 511-ISM330DHCXTR

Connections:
+3V3: C100.2, U20.1 (SDO/SA0), U20.5 (VDDIO), U20.8 (VDD), U20.12 (CS); also elsewhere on the board
/I2C0_SCL: U20.13 (SCL); also elsewhere on the board
/I2C0_SDA: U20.14 (SDA); also elsewhere on the board
/IMU_INTR1: U20.4 (INT1); also elsewhere on the board
/IMU_INTR2: U20.9 (INT2); also elsewhere on the board
GND: C100.1, U20.2 (SDx), U20.3 (SCx), U20.6 (GND), U20.7 (GND); also elsewhere on the board

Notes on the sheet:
- UMU_INTR1/2 are programmable interrupts - IMU_MODE decides operation mode of chip - use mode 1 - this is footprint compatible with other ST IMUs
**Configurable I2C address** (current 0x6B, or 0x6A if CS is pulled down)

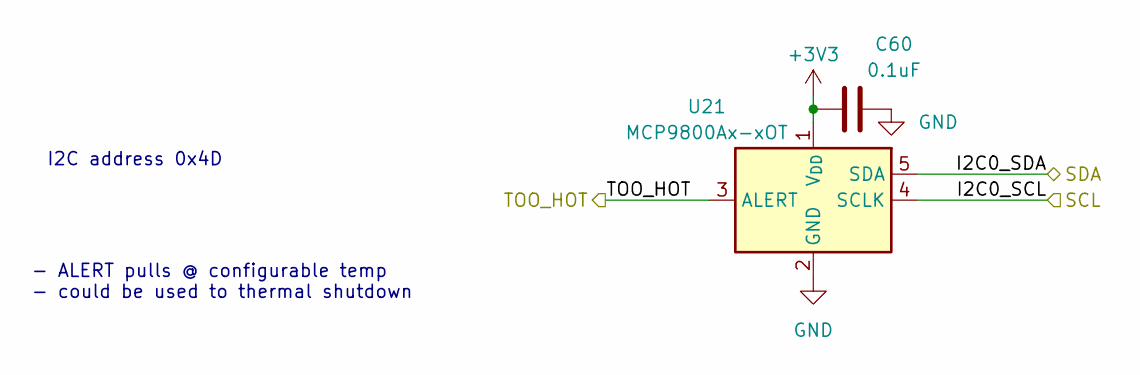
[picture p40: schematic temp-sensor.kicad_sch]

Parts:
C60: 0.1uF; C_0603_1608Metric_Pad1.08x0.95mm_HandSolder; Mouser Order Number 81-GRM155R62A104KE4J
U21: MCP9800Ax-xOT; SOT-23-5; Mouser Order Number 579-MCP9800A5T-M/OT

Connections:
+3V3: C60.1, U21.1 (V_{DD}); also elsewhere on the board
/I2C0_SCL: U21.4 (SCLK); also elsewhere on the board
/I2C0_SDA: U21.5 (SDA); also elsewhere on the board
/TOO_HOT: U21.3 (ALERT); also elsewhere on the board
GND: C60.2, U21.2 (GND); also elsewhere on the board

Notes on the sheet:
- ALERT pulls @ configurable temp - could be used to thermal shutdown
I2C address 0x4D


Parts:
C4: 100n; C_0603_1608Metric_Pad1.08x0.95mm_HandSolder
C5: 4.7n; C_0603_1608Metric_Pad1.08x0.95mm_HandSolder
D1: NUP2105L; SOT-23; MPN NUP2105L
JP2: SolderJumper_3_Open; SolderJumper-3_P1.3mm_Open_RoundedPad1.0x1.5mm
R4, R5: 60R; R_0603_1608Metric_Pad0.98x0.95mm_HandSolder
U1: TCAN3404-Q1; SOT-23-8_Handsoldering; MPN TCAN3404DDFRQ1

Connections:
+3V3: C4.2, U1.3 (VCC); also elsewhere on the board
/CAN+: D1.2 (K), R4.2, U1.7 (CANH); also elsewhere on the board
/CAN-: D1.1 (K), R5.1, U1.6 (CANL); also elsewhere on the board
/CAN_RX: U1.4 (RXD); also elsewhere on the board
/CAN_TX: U1.1 (TXD); also elsewhere on the board
GND: C4.1, C5.2, D1.3 (A), U1.2 (GND), U1.5 (SHDN), U1.8 (STB); also elsewhere on the board
unnamed: JP2.1 (A), R5.2
unnamed: JP2.3 (B), R4.1
unnamed: C5.1, JP2.2 (C)

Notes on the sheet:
CAN TRANCEIVER
Termination resistors must be very well matched to properly reject common mode noise
CAN bus operating at 1MHz 1.1MHz corner frequency R = 60 || 60 = 30 ohms T = RC = 141 ns f = 1/(2*pi*T) = 1.13 MHz
Must be rated for at least 12V
Shutdown and standby disabled Always operating in normal mode



Board: 4 copper layers, 58.5 x 57.5 mm, 111 parts (8 on the bottom side), 60 nets.

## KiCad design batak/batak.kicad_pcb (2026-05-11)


Board: 2 copper layers, 93.9 x 84.0 mm, 175 parts (0 on the bottom side), 130 nets.

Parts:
BZ1: Buzzer; CUI_CMI-1275-85T
C1, C3, C5, C8, C10, C11: 10uF; C_0603_1608Metric
C2, C4, C6: 100nF; C_0603_1608Metric
C7: 470uF; CP_Radial_D10.0mm_P5.00mm
C9: 180uF; CP_Radial_D8.0mm_P3.50mm
D1, D2, D3, D4, D5, D6, D7, D8, D9, D10, D11, D12, D14: GREEN; LED_0603_1608Metric
D13: YELLOW; LED_0603_1608Metric
D15: 1N5817; D_SOD-323F
D16: RED; LED_0603_1608Metric
D17: SS34; D_SMA
H1, H2, H3, H4: MountingHole_Pad; MountingHole_2.2mm_M2_Pad_Via
J1: XT60; AMASS_XT60PW-M_1x02_P7.20mm_Horizontal
J2, J3, J4, J5, J6, J7, J8, J9, J10, J11, J12, J13, J14, J17: Molex_KK-254; Molex_KK-254_AE-6410-04A_1x04_P2.54mm_Vertical
J15: USB_C_Receptacle_USB2.0_16P; USB_C_Receptacle_GCT_USB4105-xx-A_16P_TopMnt_Horizontal
J16: Conn_02x08_Odd_Even; IDC-Header_2x08_P2.54mm_Vertical
JP1: SolderJumper_3_Open; SolderJumper-3_P1.3mm_Open_RoundedPad1.0x1.5mm
L1: 68uH; L_Coilcraft_MSS1210-XXX
Q1, Q2, Q3, Q4, Q5, Q6, Q7, Q8, Q9, Q10, Q11, Q12, Q13: AO3400A; SOT-23
Q14, Q17: AO3401A; SOT-23
Q15, Q16: NPN; SOT-23
R1, R2, R3, R4, R5, R6, R9, R10, R13, R14, R17, R18, R21, R22, R25, R26, R27, R28, R29, R30, R31, R32, R33, R34, R35, R38, R39, R42, R43, R46, R47, R50, R51, R54, R55, R58, R59, R62, R64, R65, R72: 10k; R_0603_1608Metric
R7, R11, R15, R19, R23, R36, R40, R44, R48, R52, R56, R60, R66, R67, R71: 1k; R_0603_1608Metric
R8, R12, R16, R20, R24, R37, R41, R45, R49, R53, R57, R61: 0Ω; R_0603_1608Metric
R63, R70: 100k; R_0603_1608Metric
R68, R69, R73, R74: 5.1k; R_0603_1608Metric
RV1: 300k; TRIM_3362P-1-304LF
SW1: 0S102011MS2QN1
SW2: GAME_RESET; SW_Push_SPST_NO_Alps_SKRK
SW3: GAME_START; SW_Push_SPST_NO_Alps_SKRK
SW4, SW5, SW6, SW7, SW8, SW9, SW10, SW11, SW12, SW13, SW14, SW15: BUTTON; SW_Push_SPST_NO_Alps_SKRK
SW16: BOOT; SW_Push_SPST_NO_Alps_SKRK
SW17: RESET; SW_Push_SPST_NO_Alps_SKRK
TP1: GND; TestPoint_Pad_D1.5mm
TP2: +3V3; TestPoint_Pad_D1.5mm
TP3: +5V; TestPoint_Pad_D1.5mm
TP4: +12V; TestPoint_Pad_D1.5mm
TP5: IO0; TestPoint_Pad_D1.5mm
TP6: EN; TestPoint_Pad_D1.5mm
U1: ESP32-S3-WROOM-1
U2, U3: MCP23017_SO; SOIC-28W_7.5x17.9mm_P1.27mm
U4: CH340C; SOIC-16_3.9x9.9mm_P1.27mm
U5: XL1509-5.0; SOIC-8_3.9x4.9mm_P1.27mm
U6: AZ1117CH-3.3TRG1; SOT-223-3_TabPin2
U7, U8: SN74AHCT245NSR; NS20

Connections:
+3V3: BZ1.1 (+), C2.1, C3.2, C5.1, C11.2, D15.1 (K), D16.2 (A), R1.1, R2.2, R3.2, R4.2, R5.2, R7.2, R9.2, R11.2, R13.2, R15.2, R17.2, R19.2, R21.2, R23.2, R25.2, R26.2, R32.2, R33.2, R34.2, R36.2, R38.2, R40.2, R42.2, R44.2, R46.2, R48.2, R50.2, R52.2, R54.2, R56.2, R58.2, R60.2, R62.2, R66.2, R67.2, R73.1, R74.1, RV1.3, TP2.1, U1.2 (3V3), U2.9 (VDD), U3.9 (VDD), U4.16 (VCC), U6.2 (VO)
+5V: C10.2, J3.2, J4.2, J5.2, J6.2, J7.2, J8.2, J9.2, J10.2, J11.2, J12.2, J13.2, J14.2, J17.1, J17.3, Q14.3 (D), Q17.3 (D), TP3.1, U6.3 (VI), U7.1 (DIR), U7.20 (VCC), U8.1 (DIR), U8.20 (VCC)
+12V: C7.1, C8.1, J1.2, TP4.1, U5.1 (VIN)
/ADDRA_3V: U1.8 (IO15), U8.5 (A4)
/ADDRB_3V: U1.10 (IO17), U7.9 (A8)
/ADDRC_3V: U1.7 (IO7), U8.6 (A5)
/ADDRD_3V: U1.9 (IO16), U8.4 (A3)
/ADDRE_3V: U1.5 (IO5), U8.8 (A7)
/Arcade Button Array + Multiplexers/BTN_1_LIGHT: Q2.1 (G), R6.2, U2.28 (GPA7)
/Arcade Button Array + Multiplexers/BTN_1_OUTPUT: J3.4, R9.1, SW4.2, U2.27 (GPA6)
/Arcade Button Array + Multiplexers/BTN_2_LIGHT: Q3.1 (G), R10.2, U2.26 (GPA5)
/Arcade Button Array + Multiplexers/BTN_2_OUTPUT: J4.4, R13.1, SW5.2, U2.25 (GPA4)
/Arcade Button Array + Multiplexers/BTN_3_LIGHT: Q4.1 (G), R14.2, U2.24 (GPA3)
/Arcade Button Array + Multiplexers/BTN_3_OUTPUT: J5.4, R17.1, SW6.2, U2.23 (GPA2)
/Arcade Button Array + Multiplexers/BTN_4_LIGHT: Q5.1 (G), R18.2, U2.22 (GPA1)
/Arcade Button Array + Multiplexers/BTN_4_OUTPUT: J6.4, R21.1, SW7.2, U2.21 (GPA0)
/Arcade Button Array + Multiplexers/BTN_5_LIGHT: Q6.1 (G), R22.2, U2.8 (GPB7)
/Arcade Button Array + Multiplexers/BTN_5_OUTPUT: J7.4, R25.1, SW8.2, U2.7 (GPB6)
/Arcade Button Array + Multiplexers/BTN_6_LIGHT: Q7.1 (G), R35.2, U2.6 (GPB5)
/Arcade Button Array + Multiplexers/BTN_6_OUTPUT: J8.4, R38.1, SW9.2, U2.5 (GPB4)
/Arcade Button Array + Multiplexers/BTN_7_LIGHT: Q8.1 (G), R39.2, U2.4 (GPB3)
/Arcade Button Array + Multiplexers/BTN_7_OUTPUT: J9.4, R42.1, SW10.2, U2.3 (GPB2)
/Arcade Button Array + Multiplexers/BTN_8_LIGHT: Q9.1 (G), R43.2, U2.2 (GPB1)
/Arcade Button Array + Multiplexers/BTN_8_OUTPUT: J10.4, R46.1, SW11.2, U2.1 (GPB0)
/Arcade Button Array + Multiplexers/BTN_9_LIGHT: Q10.1 (G), R47.2, U3.28 (GPA7)
/Arcade Button Array + Multiplexers/BTN_9_OUTPUT: J11.4, R50.1, SW12.2, U3.27 (GPA6)
/Arcade Button Array + Multiplexers/BTN_10_LIGHT: Q11.1 (G), R51.2, U3.26 (GPA5)
/Arcade Button Array + Multiplexers/BTN_10_OUTPUT: J12.4, R54.1, SW13.2, U3.25 (GPA4)
/Arcade Button Array + Multiplexers/BTN_11_LIGHT: Q12.1 (G), R55.2, U3.24 (GPA3)
/Arcade Button Array + Multiplexers/BTN_11_OUTPUT: J13.4, R58.1, SW14.2, U3.23 (GPA2)
/Arcade Button Array + Multiplexers/BTN_12_LIGHT: Q13.1 (G), R59.2, U3.22 (GPA1)
/Arcade Button Array + Multiplexers/BTN_12_OUTPUT: J14.4, R62.1, SW15.2, U3.21 (GPA0)
/Auto reset/DTR: Q15.3 (E), R65.1, U4.13 (~DTR)
/Auto reset/RTS: Q16.3 (E), R64.1, U4.14 (~RTS)
/B1_3V: U1.15 (IO3), U7.4 (A3)
/B2_3V: U1.12 (IO8), U7.7 (A6)
/BUCK5V: C9.1, L1.2, Q14.2 (S), Q17.1 (G), R70.1, U5.3 (FB)
/BUZZER: Q1.1 (G), R72.2, U1.23 (IO21)
/CLK_3V: U1.11 (IO18), U7.8 (A7)
/EN: C1.2, Q16.1 (C), R3.1, SW17.1, TP6.1, U1.3 (EN)
/G1_3V: U1.17 (IO9), U7.3 (A2)
/G2_3V: U1.14 (IO20), U7.5 (A4)
/GAME_RESET: J2.1, R5.1, SW2.1, U1.31 (IO38)
/GAME_START: J2.3, R4.1, SW3.1, U1.33 (IO40)
/INT: R26.1, U1.32 (IO39), U2.19 (INTB), U2.20 (INTA), U3.19 (INTB), U3.20 (INTA)
/IO0: Q15.1 (C), R2.1, SW16.1, TP5.1, U1.27 (IO0)
/LAT_3V: U1.6 (IO6), U8.7 (A6)
/OE_3V: U1.4 (IO4), U8.9 (A8)
/P5 Display Connector + Level shifter/CLK: J16.13, U7.12 (B7)
/P5 Display Connector + Level shifter/LAT: J16.14, U8.13 (B6)
/P5 Display Connector + Level shifter/M1_A: J16.9, U8.15 (B4)
/P5 Display Connector + Level shifter/M1_B: J16.10, U7.11 (B8)
/P5 Display Connector + Level shifter/M1_B1: J16.3, U7.16 (B3)
/P5 Display Connector + Level shifter/M1_B2: J16.7, U7.13 (B6)
/P5 Display Connector + Level shifter/M1_C: J16.11, U8.14 (B5)
/P5 Display Connector + Level shifter/M1_D: J16.12, U8.16 (B3)
/P5 Display Connector + Level shifter/M1_E: JP1.2 (C), U8.12 (B7)
/P5 Display Connector + Level shifter/M1_E8: J16.8, JP1.3 (B)
/P5 Display Connector + Level shifter/M1_E16: J16.16, JP1.1 (A)
/P5 Display Connector + Level shifter/M1_G1: J16.2, U7.17 (B2)
/P5 Display Connector + Level shifter/M1_G2: J16.6, U7.15 (B4)
/P5 Display Connector + Level shifter/M1_R1: J16.1, U7.18 (B1)
/P5 Display Connector + Level shifter/M1_R2: J16.5, U7.14 (B5)
/P5 Display Connector + Level shifter/OE: J16.15, U8.11 (B8)
/R1_3V: U1.18 (IO10), U7.2 (A1)
/R2_3V: U1.13 (IO19), U7.6 (A5)
/RX0: D13.1 (K), U1.36 (RXD0), U4.2 (TXD)
/SCL: R74.2, U1.19 (IO11), U2.12 (SCK), U3.12 (SCK)
/SDA: R73.2, U1.20 (IO12), U2.13 (SDA), U3.13 (SDA)
/TOGGLE_SW: R1.2, SW1.3 (C), U1.22 (IO14)
/TX0: D14.1 (K), U1.37 (TXD0), U4.3 (RXD)
/USB5V: C6.2, J15.A4 (VBUS), J15.A9 (VBUS), J15.B4 (VBUS), J15.B9 (VBUS), Q14.1 (G), Q17.2 (S), R63.1
/USB to UART converter/USB_D+: J15.A6 (D+), J15.B6 (D+), U4.5 (UD+)
/USB to UART converter/USB_D-: J15.A7 (D-), J15.B7 (D-), U4.6 (UD-)
/VOLUME_POT: RV1.2, U1.21 (IO13)
GND: C1.1, C2.2, C3.1, C4.2, C5.2, C6.1, C7.2, C8.2, C9.2, C10.1, C11.1, D17.2 (A), H1.1, H2.1, H3.1, H4.1, J1.1, J2.2, J2.4, J3.1, J4.1, J5.1, J6.1, J7.1, J8.1, J9.1, J10.1, J11.1, J12.1, J13.1, J14.1, J15.A1 (GND), J15.A12 (GND), J15.B1 (GND), J15.B12 (GND), J15.S1 (SHIELD), J16.4, J17.2, J17.4, Q1.3 (D), Q2.2 (S), Q3.2 (S), Q4.2 (S), Q5.2 (S), Q6.2 (S), Q7.2 (S), Q8.2 (S), Q9.2 (S), Q10.2 (S), Q11.2 (S), Q12.2 (S), Q13.2 (S), R6.1, R10.1, R14.1, R18.1, R22.1, R27.2, R28.2, R29.2, R30.2, R31.2, R35.1, R39.1, R43.1, R47.1, R51.1, R55.1, R59.1, R63.2, R68.1, R69.1, R70.2, R71.2, R72.1, RV1.1, SW1.2 (B), SW1.4 (BASE), SW1.5 (BASE), SW2.2, SW3.2, SW4.1, SW5.1, SW6.1, SW7.1, SW8.1, SW9.1, SW10.1, SW11.1, SW12.1, SW13.1, SW14.1, SW15.1, SW16.2, SW17.2, TP1.1, U1.1 (GND), U1.40 (GND), U1.41 (GND), U2.10 (VSS), U3.10 (VSS), U4.1 (GND), U5.4 (~EN), U5.5 (GND), U5.6 (GND), U5.7 (GND), U5.8 (GND), U6.1 (GND), U7.10 (GND), U7.19 (*OE), U8.10 (GND), U8.19 (*OE)
unnamed: BZ1.2 (-), D15.2 (A), Q1.2 (S)
unnamed: D1.2 (A), R7.1
unnamed: D1.1 (K), Q2.3 (D), R8.1
unnamed: D2.2 (A), R11.1
unnamed: D2.1 (K), Q3.3 (D), R12.1
unnamed: D3.2 (A), R15.1
unnamed: D3.1 (K), Q4.3 (D), R16.1
unnamed: D4.2 (A), R19.1
unnamed: D4.1 (K), Q5.3 (D), R20.1
unnamed: D5.2 (A), R23.1
unnamed: D5.1 (K), Q6.3 (D), R24.1
unnamed: D6.2 (A), R36.1
unnamed: D6.1 (K), Q7.3 (D), R37.1
unnamed: D7.2 (A), R40.1
unnamed: D7.1 (K), Q8.3 (D), R41.1
unnamed: D8.2 (A), R44.1
unnamed: D8.1 (K), Q9.3 (D), R45.1
unnamed: D9.2 (A), R48.1
unnamed: D9.1 (K), Q10.3 (D), R49.1
unnamed: D10.2 (A), R52.1
unnamed: D10.1 (K), Q11.3 (D), R53.1
unnamed: D11.2 (A), R56.1
unnamed: D11.1 (K), Q12.3 (D), R57.1
unnamed: D12.2 (A), R60.1
unnamed: D12.1 (K), Q13.3 (D), R61.1
unnamed: D13.2 (A), R66.1
unnamed: D14.2 (A), R67.1
unnamed: D16.1 (K), R71.1
unnamed: D17.1 (K), L1.1, U5.2 (OUT)
unnamed: J3.3, R8.2
unnamed: J4.3, R12.2
unnamed: J5.3, R16.2
unnamed: J6.3, R20.2
unnamed: J7.3, R24.2
unnamed: J8.3, R37.2
unnamed: J9.3, R41.2
unnamed: J10.3, R45.2
unnamed: J11.3, R49.2
unnamed: J12.3, R53.2
unnamed: J13.3, R57.2
unnamed: J14.3, R61.2
unnamed: J15.A5 (CC1), R69.2
unnamed: J15.B5 (CC2), R68.2
unnamed: Q15.2 (B), R64.2
unnamed: Q16.2 (B), R65.2
unnamed: R29.1, U2.15 (A0)
unnamed: R28.1, U2.16 (A1)
unnamed: R27.1, U2.17 (A2)
unnamed: R33.1, U2.18 (~RESET)
unnamed: R32.1, U3.15 (A0)
unnamed: R31.1, U3.16 (A1)
unnamed: R30.1, U3.17 (A2)
unnamed: R34.1, U3.18 (~RESET)
unnamed: C4.1, U4.4 (V3)

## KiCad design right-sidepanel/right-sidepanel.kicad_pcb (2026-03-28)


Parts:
D1, D2, D3, D4, D5, D6: LED; LED_0603_1608Metric
F1, F2, F3, F4, F5, F6: Fuse; 01000066Z
J1: ATF13-12PA-BM01; ATF1312PABM01
J2: 43045-0412; Molex_Micro-Fit_3.0_43045-0412_2x02_P3.00mm_Vertical
J3, J4: 43045-0200; Molex_Micro-Fit_3.0_43045-0200_2x01_P3.00mm_Horizontal
J5, J6, J7, J8: S1941-42R; S194142R_THT_secured; Mouser Part Number 855-S1941-42R
R1, R2, R3, R4, R5, R6: R; R_2512_6332Metric
R7, R8, R9, R10, R11, R12: 2.2k; R_0603_1608Metric
SW1, SW2: Littelfuse 08099000

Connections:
/BSPD.PWR: J1.8, R2.2
/FS_DATALOGGER: J1.11, R3.2
/GLV_SWITCHED: F1.1, F2.1, F3.1, F4.1, F5.1, F6.1, SW1.2 (B)
/LATCHING.RESET+: J1.4, J2.2
/LATCHING.RESET-: J1.9, J2.1
/LVMP_V+: J4.2, J7.1, J8.1, R5.2
/PDM_BATT+: J1.6, J1.7, R6.2
/SDC_ORIGIN: J1.2, R1.2
/SHUT.TSAC.INTERLOCK: J1.12, SW2.1 (A)
/SHUT.TSMS: J1.1, SW2.2 (B)
/SIDE-PANEL.GND: J1.5, J4.1, J5.1, J6.1, R7.1, R8.1, R9.1, R10.1, R11.1, R12.1
/SPARE: J3.2, R4.2
/TSAL.RESET+: J1.3, J2.4
/TSAL.RESET-: J1.10, J2.3
GLV: SW1.1 (A)
unnamed: D1.2 (A), F6.2, R6.1
unnamed: D1.1 (K), R7.2
unnamed: D2.2 (A), F5.2, R5.1
unnamed: D2.1 (K), R8.2
unnamed: D3.2 (A), F4.2, R4.1
unnamed: D3.1 (K), R9.2
unnamed: D4.2 (A), F3.2, R3.1
unnamed: D4.1 (K), R10.2
unnamed: D5.2 (A), F2.2, R2.1
unnamed: D5.1 (K), R11.2
unnamed: D6.2 (A), F1.2, R1.1
unnamed: D6.1 (K), R12.2

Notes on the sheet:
Fuse Debug LEDs
LVMP GND
LVMS
Reset Button
LVMP V+


Board: 2 copper layers, 150.0 x 83.0 mm, 34 parts (0 on the bottom side), 26 nets.

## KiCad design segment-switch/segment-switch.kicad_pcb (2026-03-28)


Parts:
H1, H2: MountingHole; MountingHole_3.2mm_M3
J1: Conn_01x02; Conn2_SMD
SW1: SW_SPST; 24549852

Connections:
unnamed: J1.1, SW1.B1 (B)
unnamed: J1.2, SW1.A1 (A)


Board: 2 copper layers, 20.0 x 31.2 mm, 4 parts (0 on the bottom side), 2 nets.

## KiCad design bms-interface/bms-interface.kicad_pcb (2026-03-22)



Board: 2 copper layers, 145.0 x 10.0 mm, 13 parts (2 on the bottom side), 4 nets.

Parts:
H3, H5: MountingHole; MountingHole_4.3mm_M4
J1: CAN_Upstream; Molex_Micro-Fit_3.0_43045-0412_2x02_P3.00mm_Vertical
J2: CAN_Downstream; Molex_Micro-Fit_3.0_43045-0412_2x02_P3.00mm_Vertical
Segment1, Segment2, Segment3, Segment4, Segment5, Segment6, Segment7, Segment8, Segment9: Molex 43045-0412; Molex_Micro-Fit_3.0_43045-0412_2x02_P3.00mm_Vertical

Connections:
+12V: J1.2, J2.2, Segment1.2, Segment2.2, Segment3.2, Segment4.2, Segment5.2, Segment6.2, Segment7.2, Segment8.2, Segment9.2
/CAN+: J1.3, J2.3, Segment1.3, Segment2.3, Segment3.3, Segment4.3, Segment5.3, Segment6.3, Segment7.3, Segment8.3, Segment9.3
/CAN-: J1.4, J2.4, Segment1.4, Segment2.4, Segment3.4, Segment4.4, Segment5.4, Segment6.4, Segment7.4, Segment8.4, Segment9.4
GND: J1.1, J2.1, Segment1.1, Segment2.1, Segment3.1, Segment4.1, Segment5.1, Segment6.1, Segment7.1, Segment8.1, Segment9.1

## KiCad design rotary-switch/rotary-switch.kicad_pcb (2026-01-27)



Board: 2 copper layers, 36.0 x 42.0 mm, 22 parts (6 on the bottom side), 15 nets.

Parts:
C1: 1u; C_0805_2012Metric
C2: 10uF; C_0805_2012Metric
C3: 4.7uF; C_0805_2012Metric
D1: 1N5711W; D_SOD-123
H1, H2, H3, H4: MountingHole_Pad; MountingHole_3.2mm_M3_DIN965_Pad
J1: Conn_01x04_Socket; Molex_Micro-Fit_3.0_43045-0412_2x02_P3.00mm_Vertical
R1, R2, R3, R4, R5, R6, R7, R8, R9, R10, R11: 330; R_0805_2012Metric
SW1: SW_Rotary_1x12; ALPHA_12pos_rotary
U1: TPS7B6925-Q1; SOT-23-5_HandSoldering

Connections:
+3V3: C3.1, R1.1, SW1.1, U1.5 (OUT)
+GLV: D1.2 (A), J1.1
/Output: C1.1, J1.2, SW1.13
GND: C1.2, C2.2, C3.2, H1.1, H2.1, H3.1, H4.1, J1.4, R11.2, SW1.12, U1.3 (GND), U1.4 (GND)
unnamed: C2.1, D1.1 (K), U1.1 (IN)
unnamed: R1.2, R2.1, SW1.2
unnamed: R2.2, R3.1, SW1.3
unnamed: R3.2, R4.1, SW1.4
unnamed: R4.2, R5.1, SW1.5
unnamed: R5.2, R6.1, SW1.6
unnamed: R6.2, R7.1, SW1.7
unnamed: R7.2, R8.1, SW1.8
unnamed: R8.2, R9.1, SW1.9
unnamed: R9.2, R10.1, SW1.10
unnamed: R10.2, R11.1, SW1.11

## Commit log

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2022-11-18 feat(vcu): first draft of schematic (#17)
    * chore: ignore autosaves in .gitignore
    * feat(lib): add MAX33040E symbol and footprint
    * feat(vcu): change CAN transceiver to MAX33040E
    * feat(vcu): update MCU to STM32 F746ZG
    * feat(lib): add M24256-A125 EEPROM symbol and footprint
    * feat(vcu): add EEPROM to schematic
    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
    [can-transceiver.kicad_sch, drs-driver.kicad_sch, input-shift.kicad_sch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]
2022-11-26 feat(vcu): final draft of schematic (#18)
    * feat(vcu): add shutdown pin
    * feat(lib): add FDN359BN MOSFET symbol
    * feat(vcu): add variable resistor and new MOSFET to speaker driver
    * fix(vcu): annotate MCU pins with text instead of labels
    fixes about 80 ERC warnings
    * fix(vcu): add exception to ERC for RTDS+ / 12V connection
    * fix(vcu): remove PWR_FLAG from DRS regulator
    * feat(vcu): add optional pull up resistors to set I2C bus time constant
    * feat(lib): add TSSOP-8_3x6.4mm_P0.65mm footprint and 3D model
    * feat(vcu): update EEPROM model and footprint
    * feat(vcu): add 3.3V power connections from MCU
    * feat(vcu): remove old indicator LEDs
    can use those built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
    [TSSOP-8_3x6.4mm_P0.65mm.step, analog-input-shift.kicad_sch, can-transceiver.kicad_sch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]
2022-11-26 feat(vcu): add footprints for all components (#19)
    * chore(vcu): reset footprints
    * feat(vcu): add footprint for EEPROM
    * feat(vcu): add footprint and 3D model for optocouplers
    * feat(vcu): add footprint for speaker FET
    * feat(vcu): add footprint for DRS 5V regulator
    * feat(vcu): add footprints and specs for capacitors
    * feat(vcu): add footprints for zener diodes
    * feat(vcu): add footprint for mounting holes
    * feat(vcu): add footprints and specs for fixed resistors
    * feat(vcu): add footprints for MCU pin sockets
    * feat(vcu): make RTD speaker resistor optional
    * feat(vcu): add power LED footprint
    * refactor(vcu): use only 4 and 2 pin connectors
    * feat(vc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
    [ILQ615-4X009T.step, can-transceiver.kicad_sch, input-shift.kicad_sch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]
2022-12-01 feat(vcu): complete PCB layout (#20)
    * chore(vcu): clear out outdated components in layout
    * feat(vcu): add footprint for testpoints (draft)
    * feat(vcu): add footprint for DRS 5V level shifter
    * feat(vcu): lay out MCU sockets
    * feat(vcu): first draft of most placement and routing
    * feat(lib): add SUFST and Stag logo footprints
    * feat(vcu): add SUFST logos to silkscreen
    * feat(vcu): compactify layout of input side
    * feat(vcu): add 3D models
    * feat(vcu): complete draft of layout
    * feat(vcu): add 3D models for Molex Microfit connectors
    * fix(vcu): make absolute paths relative
    * fix(vcu): make more absolute paths relative
    * feat(vcu): improve routing of 12V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
    [3214W-1-102G.stp, Molex-MicroFit-436500200.stp, Molex-MicroFit-436500215.stp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]
2022-12-04 feat(segment): create segment PCB (#21)
    * feat(segment): create schecmatic for segment connections
    * feat(lib): add Littelfuse 04611.25ER footprint
    * feat(segment): assign footprints
    * feat(segment): first attempt at layout
    * feat(segment): add 3D models
    * feat(segment): add labels to silkscreen
    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
    [Littelfuse-04611-25ER.step, Molex-MicroFit-430251400.stp, Molex-MicroFit-430252400.stp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]
2022-12-04 feat(tsal): update TSAL driver (#23)
    * new tsal driver pcb to connect between the leds and the hv-sense pcb
    * feat(tsal): updated schematic and pcb
    * feat(tsal) added cad files for the connectors and comments to the schematics
    * feat(tsal) updated tsal driver pcb design: changes in routing, added 12V power plane, added via for Q2, made board smaller, hid mounting hole reference names, moved cad files into common, swapped green_led_on and red_led_on pins for simpler routing, added board name to board, moved symbols library from global to project specific
    * feat(tsal): minor adjustments to silkscreen positioning
    * fix(tsal): make 3D model paths relative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
    [Molex-MicroFit-436500315.stp, tsal.kicad_pcb, tsal.kicad_sch]
2022-12-15 chore: clean up repo (#24)
    * feat(bspd) added footprints, datasheets and order codes for all components. fixed erc. some terminals need to be marked as NC as drc keeps alerting to warnings
    * chore(all) renamed BSPD files to remove version number from name, moved all symbols from individual symbol libraries into common/sufts-lib.kicad_sym, combined all project specific footprint folders into common/sufts-lib.pretty, moved all project specific step files into common/step, fixed all paths making them relative, fixed all broken cad models on pcbs. missing one cad model that is simply impossible to find online. imported discharge relay breakout pcb folder.
    * fixed all sheet formats for all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
    [3362P-1-304LF.step, BSPD.kicad_pcb, BSPD.kicad_sch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]
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2023-01-28 fix(segment): increase trace widths of voltage taps (#27)
    * fix(segment): increase trace width for voltage taps
    * refactor(segment): improve various bits of routing
    [segment.kicad_pcb]
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2023-02-02 feat(tsal): completed pcb schematic and layout (#30)
    * feat(tsal): completed psc schematic and layout
    * fix(tsal): corrected a few power connection issues
    * fix(tsal): update layout with schematic changes
    * feat(tsal): finalise layout
    * feat(tsal): Added some 3D models
    * fix(tsal): update power symbols to stop ERC error
    * feat(tsal): update sheet info
    ---------
    [tsal.kicad_pcb, tsal.kicad_sch]
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2023-02-03 feat(bspd): completed layout (#32)
    * test
    * fixed all shee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
    [BSPD.kicad_pcb, BSPD.kicad_sch, brake-plausibility.kicad_sch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]
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2023-02-04 fix(tsal): increase number of LED connections (#35)
    * fix(tsal): increase number of LED connections
    * feat(tsal): make LED connections visually clearer
    [Molex-MicroFit-430450812.stp, tsal.kicad_pcb, tsal.kicad_sch]
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2023-02-04 fix(tsal): update dimension drawings for release v1.1.4
    [tsal.kicad_pcb]
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2023-02-04 fix(tsal): resize switched ground plane (#39)
    [tsal.kicad_pcb, tsal.kicad_sch]
2023-02-04 fix(bspd): corrected connector footprints (#42)
    [BSPD.kicad_pcb, BSPD.kicad_sch, brake-plausibility.kicad_sch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]
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2023-02-06 fix(tsal): added missing 3D models (#44)
    [Littlefuse-395Series.stp, tsal.kicad_pcb]
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2023-03-01 fix(vcu): drive output optocoupler signals at 12V instead of 3.3V (#57)
    [can-transceiver.kicad_sch, input-shift.kicad_sch, mcu.kicad_sch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]
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2023-03-05 feat(vcu): layout for v1.2.0 (#62)
    * feat(vcu): layout for v1.2.0
    * fix(vcu): remove accidental extra label on silkscreen
    * fix(vcu): update incorrect silkscreen pin label
    [Molex-MicroFit-430250400.stp, Molex-MicroFit-430450400.stp, can-transceiver.kicad_sch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]
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2023-04-01 fix(latching): corrected latching behaviour (#75)
    * fix(latching): corrected latching behaviour
    * chore(latching): rename files
    * docs(latching): improve annotations
    [latching.kicad_pcb, latching.kicad_sch]
2023-04-01 fix(vcu): improve safety of input stages (#77)
    * feat(vcu): pull down digital inputs
    * feat(vcu): add filters and pulldown to analogue inputs
    [input-shift.kicad_sch, vcu.kicad_sch]
2023-04-02 feat(latching): revised layout for fixed latching logic (#76)
    feat(latching): revised layout for new latching logic
    [latching.kicad_pcb, latching.kicad_sch]
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2023-04-02 feat(hvs): add fusing and adjust resistor values (#79)
    * feat(hvs): add fusing to HV input
    * feat(hvs): round the board edges
    * feat(hvs): minor silkscreen adjustments
    * feat(hvs): add silkscreen labels for connectors
    * feat(hvs): downsize precharge relay contact wetting resistor
    * feat(hvs): add project name and version to silkscreen
    * feat(hvs): add wek pull downs to logic inputs
    * feat(hvs): add fuse to TS side 12V
    * fix(hvs): add missing power flag
    [hv_sense.kicad_pcb, hv_sense.kicad_sch, logic.kicad_sch]
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2023-04-03 fix(bspd): improve layout and fix connection issues (#74)
    * fix(bspd): increase low SCS threshold
    * fix(bspd): add missing IC power connection to schematic
    * fix(bspd): update footprint and minimise layout
    * fix(bspd): change SCS error LED colour
    * fix(bspd): increase mounting hole size to M3
    * feat(bspd): replace connectors with solder pads
    * feat(bspd): add labels to potentiometers
    * feat(bspd): add PCB dimensions
    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
    [BSPD.kicad_pcb, BSPD.kicad_sch, brake-plausibility.kicad_sch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]
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2023-04-04 feat(telemetry): initial PCB design (#52)
    * first commit telemetry pcb
    * added xbee subschematic and new connections
    * annotations
    * Updated MCU file to be Nucleo-446RE
    * NUCLEO F446RE model
    * nucleo footprint
    * fixed footprint and group
    * components org
    * added MCU pins and GPS
    * routing
    * 3d files and view
    * chore: add sheet information
    * fix(telemetry): corrected some ERC issues
    * docs: add telemetry to README
    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
    [AntennaConnector.step, BM61276.STEP, GPS.kicad_sch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]
2023-04-04 feat(telemetry): add 7 segment display driver (#86)
    * fix(telemetry): corrected Tx and Rx connections to CAN transceivers
    * fix(telemetry): corrected layout of CAN transceivers
    * feat(telemetry): add dash LED driver
    * feat(telemetry): finalise layout and silkscreen
    [MAX6955.step, MAX6958BAEE_T.step, NEO-M9N.stp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]
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2023-04-18 feat(ail): create AIL PCB (#93)
    * tsac pcb created
    1st revision
    * small tweaks
    * broke something
    kicad didn't like git
    * v1.0.0
    added 2 more mosfets in parallel
    some silkscreen tweaks
    thicker traces
    * minor changes
    swapped connector footprints
    * chore: rename TSAC to AIL
    * docs: add AIL project to README
    * chore(ail): update sheet information
    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
    [Molex-MicroFit-436500214.stp, ail.kicad_pcb, ail.kicad_sch]
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2023-04-25 feat(ail): add copper pour to MOSFET drains (#95)
    * Added copper pour to Q1-drain, removed R1
    * fix(ail): remove track stubs
    * wip(ail): attempt to fix clearance issues
    not successfully...
    * fix(ail): corrected clearance violation for isolation slot
    * fix(ail): removed thermal relief for mosfet pour, increased size slightly
    * fix(ail): replaced out of stock components
    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
    [ail.kicad_pcb, ail.kicad_sch]
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2023-04-25 feat(test): initial design for test rig (#97)
    * feat(test): initial design for test rig
    * feat(test): add 3D models
    * wip(test): minor tweaks
    * feat(test): tidy up schematic
    * feat(test): setup bus definitions
    * feat(test): add visual check circuitry
    * fix(test): add missing footprint to SUFST library
    * feat(test): finalise silkscreen
    * fix(test-rig): swapped mosfets on VCU LEDs
    * feat(test): final tweaks
    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
    [ALPS-RK09K.step, OS102011MS2QN1.step, RD902F-40-00D.step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]
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2023-04-27 feat(trc): full redesign with pre-charge controlled by inverter (#89)
    * feat(precharge): first draft of schematic for inverter controlled design
    * feat(precharge): pull down 'TS on' and 'external fault' inputs
    * docs(precharge): add some extra schematic comments
    * feat(precharge): remove inverter ignition circuit
    should be outside TSAC
    * feat(precharge): improve safety of external fault input
    * feat(precharge): add logic for interfacing with BMS
    * feat(precharge): first draft of new layout
    * feat(precharge): round the board edges
    * feat(precharge): remove track stubs
    * feat(precharge): add mounting holes
    * feat(precharge): finalise board dimensions
    * fix(p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
    [Molex-MicroFit-430250200.stp, Molex-MicroFit-430450200.stp, Molex-MicroFit-430450212.stp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]
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2023-04-27 release(trc): v1.0.0 (fixed gerbers)
    [trc.kicad_pcb]
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2023-04-29 feat(loom): initial loom design (#98)
    * feat(Loom): initial loom design
    * chore(Loom): removed items that shouldnt be in folder
    * fix(Loom): made requested changes + chores
    * fix(Loom): changed position of components
    * feat(loom): minor tweaks to dash + VCU connections
    * chore(loom): rename folder for consistency
    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
    [Accumulator.kicad_sch, Dash Box.kicad_sch, Ground Box.kicad_sch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]
2023-04-29 feat(discharge): redesigned discharge + chores (#107)
    * feat(Discharge): Redesigned Discharge pcb + chores
    * fix(Discharge): final fixes
    * fix(discharge): minor tweaks to silkscreen
    also typos on sheet info
    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
    [Discharge.kicad_pcb, Discharge.kicad_sch, discharge-relay-breakout.kicad_pcb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]
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2023-05-11 fix(hvs): seperated HV input connection (#108)
    * fix(HV_Sense): seperated HV in connection
    * fix(Hv_Sense): fixed hv spacing issues
    * fix(Hv_Sense): fixed drc issues
    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
    [hv_sense.kicad_pcb, hv_sense.kicad_sch]
2023-05-11 release(hvs): v1.1.1 (#110)
    * release(Hv_Sense): release for Hv_sense v1.1.1
    * fix(Hv_Sense): fixed info document
    * fix(Hv_Sense): fixed schematic document
    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
    [hv_sense.kicad_pcb, hv_sense.kicad_sch, logic.kicad_sch]
2023-05-11 release(discharge): v1.1.0 (#111)
    * release(discharge): release for discharge
    * fix(Hv_Sense): fixed fabrication document
    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
    [Discharge.kicad_pcb]
2023-08-24 feat(Loom) - Updated Schematic (#114)
    * fix(Loom): changed names of netlists
    * feat(Loom): Updated version of Loom Schematic
    * feat(Loom): Minor changes to schematic
    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
    [Accumulator.kicad_sch, Dash Box.kicad_sch, DashBoard.kicad_sch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]
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2023-08-26 chore(Loom): Fixing mistake made in previous commit conserning 'ground box.kicad_sch'
    [DashBoard.kicad_sch, Ground Box.kicad_sch, Loom.kicad_pcb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]
2023-08-31 Added message about missing clamp on non-inverting input of op-amp
    [ail.kicad_sch]
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2024-01-12 Removed slot (PCB edge might not be isolated, so slot could violate clearance to alu board)
    [ail.kicad_pcb]
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2024-02-11 TSAL fixes
    [tsal.kicad_pcb]
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2024-03-15 Fixed connector STEP files
    [BSPD.kicad_pcb, Discharge.kicad_pcb, ail.step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]
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2024-09-23 release(new-ail): v1.2.0 (#118)
    * Added potential diode part number
    * TVS alternative - TODO add the protection and incorporate the mosfet
    * Updated AIL with TVS and new layout.
    Larger MCPCB for better heat dissipation, added TVS and lowpass filter to prevent voltage spike from killing components.
    * Fixed board edge
    * Delete release/discharge/Fabrication.zip
    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
    [ail.kicad_pcb, ail.kicad_sch]
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2024-09-26 Squashed commit of the following:
    commit b405d24fe3f4403e9168e939b6071bdab96ec8ab
    Author: Ray Wang <jcw1g22@soton.ac.uk>
    Date: Thu Sep 26 11:44:22 2024 +0100
    Fixed fab file locations
    commit 918672a0833823f4ce97bd685076c57d29a1cbbf
    Author: Ray Wang <jcw1g22@soton.ac.uk>
    Date: Thu Sep 26 11:28:48 2024 +0100
    Fab files ready
    generated using Fabrication Toolkit
    commit 52939e68da55589a094887908e21b7a594cf9f38
    Author: Ethan Turnbull <121163204+brad-berry@users.noreply.github.com>
    Date: Mon Sep 23 10:53:17 2024 +0100
    Delete release/discharge/Fabrication.zip
    commit 3d8bf0cf2a690045810896ee103ba37f42dba2d8
    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
    [ail.kicad_pcb, ail.kicad_sch]
2024-09-26 release(ail): v1.2.0 (#121)
    * Fab files ready
    * Fixed fab file locations
    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
2024-11-19 Add strain gauge amp breakout board (#122)
    * Sensor Board preliminary design
    wheatstone bridge my beloved
    * move sensor-board/ to sensor-board/rays-attempt
    * add v1.0 of strain gauge breakout board
    * add part urls list
    * fix broken urls
    * add 10uF decoupling capacitor and connector for strain gauge pot
    * wip
    * refactor libraries and add release files
    * Updated board layout
    * update silkscreen
    * fix a few issues
    * update release to latest board version
    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
    [sensor-board.kicad_pcb, sensor-board.kicad_sch, strain-gauge-amp-breakout.kicad_pcb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]
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2024-12-12 Improvement to TRC
    Added Green Led, correct power and SS relays
    [control.kicad_sch, relays.kicad_sch, trc.kicad_pcb]
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2025-02-06 Updated to correct schematic
    [tsal-led.kicad_pcb, tsal-led.kicad_sch]
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2025-02-15 Revert "Merge branch 'main' into tsal-led"
    This reverts commit b8431bf9aab271a0ae3b7bb2565335d31a772841, reversing
    changes made to 2533238e78a0882b7119c906f24b373fa21a2f26.
    [ail.kicad_sch, can-node.kicad_pcb, can-node.kicad_sch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]
2025-02-15 TSAL LED Release
    * start of tsal LED design
    * Add files via upload
    * Add files via upload
    * New project filepaths, updated libraries
    * lockfiles my beloved
    * Updated to correct schematic
    * PCB design 40%
    * Added inductor, finialised board layout
    * Simulations!
    * Simulations were attempted
    It was not fine
    * Updated to take EN signal instead of TSAL sink
    * RELEASE YAY
    * Revert "Merge branch 'main' into tsal-led"
    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
    [43650-0410.stp, LMR33620CQRNXRQ1.stp, TSAL-LED.kicad_pcb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]
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2025-03-04 Fixed CAN pinout, added wire slots
    [bms-interface.kicad_pcb, bms-interface.kicad_sch]
2025-03-05 Fixed Silkscreen marks
    [bms-interface.kicad_pcb, segment-taps.kicad_sch]
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2025-03-23 Fixed files reverted in 01bbc30
    [ail.kicad_sch, can-node.kicad_pcb, can-node.kicad_sch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]
2025-03-26 fix(actions): ERC warnings due to missing lib tables and errors due to running on child schematics (#133)
    Fix ERC warnings caused by missing lib tables and errors due to running on child schematics
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2025-04-27 Added bodge wire
    [tsal-led.kicad_sch]
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2025-04-29 Dash v2.0.0 (#136)
    * Dash2024
    * Feat: Schematic updates
    5V linear regulator
    CAN_RX/TX changes
    Screen UART communication
    Programming pins
    * Updates to Schematic
    * Schematic changes
    * More schematic chnages
    * Made footprints, loaded footprints onto pcb layout, fixed some flag errors
    * update
    * 04022025
    rearranged the components
    haven't routed yet
    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
    [Dash-PCB-TFTscreen.kicad_sch, Dash-PCB.kicad_pcb, Dash-PCB.kicad_sch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]
2025-05-06 Feat/tidy actions (#138)
    * fix(actions): Overwrite existing tag numbers rather than erroring when generating production files
    * move scripts from ./bin to github.com/sufst/sufst-scripts
    * Only test changes on [push] rather than [push, pull_request] since pull requests will be checked anyway when changes are added
    * Generate drill files as well as gerbers
    * refactor actions to use composite container actions which makes everything 3x faster and more modular (so easier to read)
    * edit initial suggestion message if PR is updated
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2025-06-20 Added bodge to fix high impedance
    The TRC has logic gates powered both by 12V from the shutdown and 12V from the tsal battery, the addition of these pulldowns prevent high impedance inputs to the green light logic
    [control.kicad_sch]
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2025-09-25 Fixed CAN-S bodge
    v1.5.0
    Update to KiCad 9
    [GPS.kicad_sch, can-transceiver.kicad_sch, input-shift.kicad_sch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]
2025-09-25 Fixed VCU CAN-S bodge
    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
    [GPS.kicad_sch, can-transceiver.kicad_sch, input-shift.kicad_sch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]
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2025-10-07 Revert "Added GPS to repo"
    This reverts commit ecedf19d310c8a691bcee37a5232e1221735b3e5.
    [GPS.kicad_pcb, GPS.kicad_sch, SparkFun_GPS_ZED-F9K.kicad_pcb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]
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2025-12-04 Started PCB layout
    TODO:
    - Verify inductor won't blow up
    - Thermal calcs
    - Does current path make sense?
    [tsal-led.kicad_pcb, tsal-led.kicad_sch]
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2026-01-21 Update SHF10501LDTHLC.kicad_mod
    Decreased the size of the PTH so that it is within AISLER tolerances
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2026-01-24 Can Repeater v1.1.0 Release (#145)
    This commit releases the design (Schematic, PCB, and Production files) for the CAN Repeater module.
    The device is designed to receive messages on one CAN bus and forward them to a secondary bus, acting as a bridge/extender.
    Hardware Specifications:
    - MCU: STM32F105RBT6
    - Connectors: Harwin Datamate connectors selected for high-vibration reliability, and ease crimping.
    - Power: Wide input range (12-24V) stepped down via a simple buck converter to 3.3V.
    - Programming: Standard 1.27mm 10-pin ARM SWD header.
    - Interface: 3x User/Status LEDs, USART/Spare GPIO
    - Loom: Daisy chainable CANH and CANL on booth sides. Power in on one side.
    Mechanical:
    - Small form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
    [ABM8AIG-8.000MHZ-1Z-T.stp, Dash-PCB.kicad_pcb, Dash-PCB.kicad_sch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]
2026-01-25 Release CAN Repeater v1.2.0 (#146)
    * Started project
    * pcb placement
    * Nearly Finished PCB design
    * Reviewing Changes
    * Finished CAN-Repeater
    * Added Quote and Fuse
    * Added harwin connectors and aisler logo area
    Also changed to M2 screws, and added teardrops
    * Generate Ibom
    * Release CAN-Repeater v1.0.0
    * Release can-repeater v1.0.1
    Changed reverse protection component
    * Forgot to generate BOM
    * moved ibom to correct release folder
    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
    [can-repeater-B_Cu.gbr, can-repeater-B_Mask.gbr, can-repeater-B_Paste.gbr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]
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2026-01-27 Release BSPD v1.3.0 (#149)
    * Create BSPD for Stag12 Redesign
    * BSPD_sig_explain.xlsx
    * Update BSPD_sig_explain.xlsx
    * testkit added
    * Update BSPD_sig_explain.xlsx
    * Update BSPD_testkit.kicad_sch
    * DONE FINALLY (bspd testkit)
    * Moved test rig changes to new branch
    Also moved xlsx to sharepoint
    * Added input buffer to BSPD
    * Synced TLV9104 files
    * TLV9104 symbol
    * TLV9104 symbol creation
    * v1.3.0 Prerelease
    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
    [43025-1200.stp, 43045-1200.stp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]
2026-01-27 Re-Release Rotary Switch v1.0.0 (#151)
    * Reset branch to main base, preserved rotary-switch folder
    * Lets try this again
    * Retain common folder from dash branch
    * Update silkscreen
    * Re-Release Rotary-Switch v1.0.0
    Nothing chnaged other than to fix silkscreen clipping
    * Git is a nightmare
    [rotary-switch-B_Cu.gbr, rotary-switch-B_Mask.gbr, rotary-switch-B_Paste.gbr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]
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2026-02-24 Fix LDO value
    [rotary-switch.kicad_sch]
2026-03-22 TEM CAN Interface v1.2.0 Release (#153)
    * Changed to THT headers, added 9th segment
    * Rough layout finalised
    * Change to panel mount Molex
    * Updated V1.1.2 Layout
    Placed connectors closer, added CAN up/downstream connectors
    * Moved CAN bus connections to end of PCB
    TODO: Verify stacking PCBs will not affect signals
    * v1.1.4 Prerelease
    Lowered mounting holes
    * Update to only have CAN, move BMS taps to loom
    * v1.2.0 Release
    * Fix silkscreen labels, and generate new production files
    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
    [43020-1400.stp, CAN_breakout.kicad_sch, bms-interface.kicad_pcb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]
2026-03-28 Release Segment Switch v1.0.0 (#155)
    * v1.0.0 prerelease
    * v1.0.0 Release
    * Fix dodgy shit
    * Fixed STEP and silkscreen
    * Generate production files and rename project
    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
    [2454985-2.stp, segment-scs-switch_v1.0.0.step, segment-switch.kicad_pcb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]
2026-03-28 Release Right Sidepanel v1.2.0 (#156)
    * Created LVMS footprint, added fuse holder
    just one more PCB...
    * v1.1.0
    Added blade fuse springs, LED indicators for fuses
    * v1.2.0
    * Adde silkscreen
    * Updated library
    Just one more PCB
    * change filenames
    * Fixed ERC errors
    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
    [01000066Z.stp, AT06-12SA.stp, Fuse_Littelfuse_02870_Series_ATOF_Blade_Automotive.STEP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]
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2026-06-12 Sensor Hub 1.2.0 Release (#154)
    * progress from last week
    * temp update
    To find GND issue
    * Current Design 18/11/25
    Current agreed design at the time of EOS, by Adam and Ray contributions
    * Update library paths and clean up PCB net segments
    Replaced absolute library paths with project-relative variables in fp-lib-table and sym-lib-table for improved portability. Removed redundant or unnecessary traces.
    * Add fuses and update connector/capacitor references
    Added Device: Fuse symbols and instances to the schematic for overcurrent protection. Updated connector and capacitor reference designators and locations, and extended several nets to new connectors and components for improved organ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
    [16Ch-Sensor-Hub.kicad_pcb, 16Ch-Sensor-Hub.kicad_sch, 43025-0400.stp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]
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2026-06-14 correct TSMS naming on RSP pcb
    [right-sidepanel.kicad_sch]
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

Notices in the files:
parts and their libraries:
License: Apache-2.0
